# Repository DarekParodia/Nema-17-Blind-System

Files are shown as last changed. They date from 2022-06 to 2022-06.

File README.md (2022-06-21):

# Nema-17-Blind-System
I made my own system, for controling window blinds, using **Nema 17** stepper motor, and **a4988** stepper driver.
Design involves 3d printing, and making homemade pcb, or just using unviersal one.
Blinds can be easly controlled either by buttons or external hardware. PCB has 5 pins coming out of it, which has all the voltages and button pins coming in to microcontroller.
To connect motor to the pcb i used 2mm goldpins, because my motor has this type of connector.
You can drive blinds using gearbox, it depends on how heavy your blinds are, or how strong is your motor.
Design uses M3 screws to assembly everything. I didn't put points for screwing the pcb so you can attach it anyway you want

STL files can be found also on thingiverse: https://www.thingiverse.com/thing:5415491

# 🛠 Needed Parts
- 1x Nema 17 motor
- 1x a4988 driver
- Switches
    - 2x microswitch
    - 1x quad dip switch
- IC
    - 1x attiny 13
    - 1x lm7805
- Connectors
    - 1x quad goldpins (2mm)
    - 1x fivefold goldpins (2,54mm)
    - 1x dc jack (5.5mm)
- 2x capacitor (12v 100f)
- resistors
    -  2x 1 kΩ
    -  1x 470 Ω
- 1x 3mm led
- 1x 62x42 mm pcb  
- 12v power supply 1A (motor don't needs that much power but it's better to have more)
# 🔧 Assembly
- 3d print all needed parts
    - motor mount
    - blind holder
    - gearbox (Optional)
- screw motor to the motor mount (Optional: screw it with the gearbox)
- put on the tip blind holder
- screw all thing to the wall

# 🧩 Code
coming soon

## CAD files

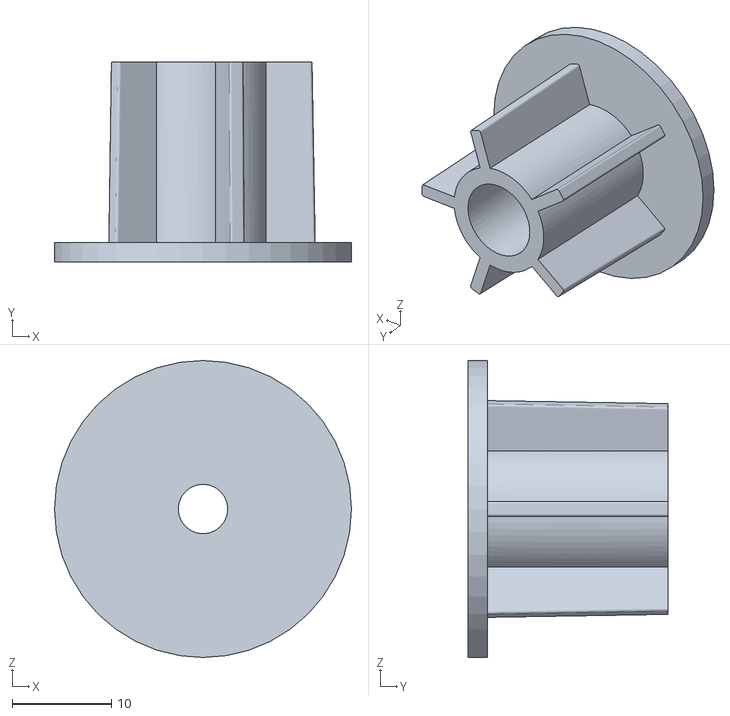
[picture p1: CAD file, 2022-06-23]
STL files/Blinds Holder v2.obj
30.0 x 20.3 x 30.0

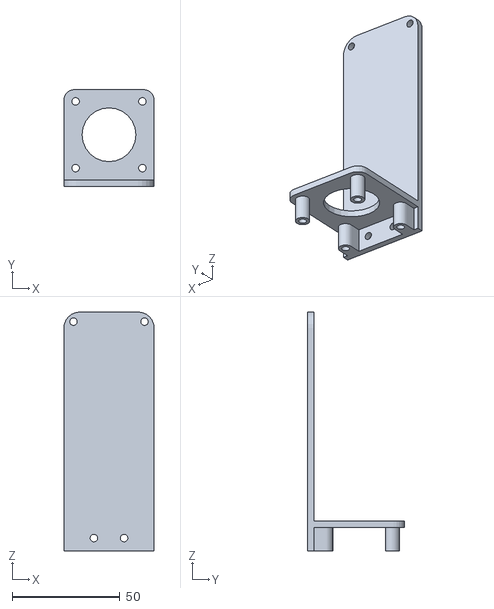
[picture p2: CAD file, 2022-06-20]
STL files/MotorMount v2.obj
42.0 x 45.0 x 111.0

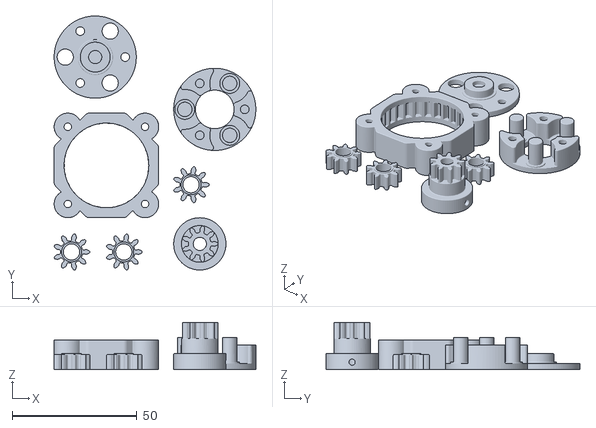
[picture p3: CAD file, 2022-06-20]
STL files/Planetary_Gearbox_v5_sep.stl
81.0 x 102.0 x 19.0

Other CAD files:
Fusion 360 files/MotorMount v2.f3d

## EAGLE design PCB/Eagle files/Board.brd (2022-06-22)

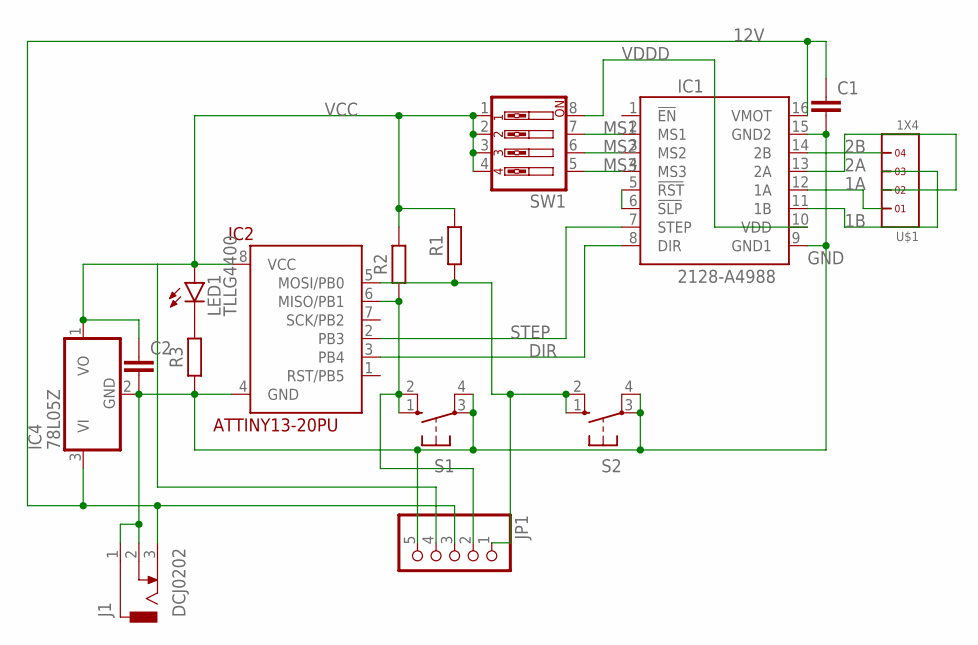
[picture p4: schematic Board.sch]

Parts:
C1, C2: C2.5/6; C2.5-6
IC1: 2128-A4988; A4988
IC2: ATTINY13-20PU; DIL08
IC4: 78L05Z; TO92
J1: DCJ0202
JP1: PINHD-1X5; 1X05
LED1: TLLG4400; LED3MM
R1, R2, R3: R_AXIAL-7.2MM-PITCH; RESAD724W46L381D178B
S1, S2: 10-XX; B3F-10XX
SW1: SW_DIP-4; EDG-04
U$1: 1X4

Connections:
1A: IC1.12 (1A), U$1.1
1B: IC1.11 (1B), U$1.3
2A: IC1.13 (2A), U$1.2
2B: IC1.14 (2B), U$1.4
12V: C1.1, IC1.16 (VMOT), IC4.3 (VI), J1.3, JP1.3
DIR: IC1.8 (DIR), IC2.3 (PB4)
GND: C1.2, C2.2, IC1.9 (GND1), IC1.15 (GND2), IC2.4 (GND), IC4.2 (GND), J1.1, J1.2, JP1.5, R3.1, S1.3, S1.4 (P1), S2.3, S2.4 (P1)
MS1: IC1.2 (MS1), SW1.7
MS2: IC1.3 (MS2), SW1.6
MS3: IC1.4 (MS3), SW1.5
unnamed: LED1.K (C), R3.2
unnamed: IC2.5 (MOSI/PB0), JP1.1, R1.1, S2.1 (S), S2.2 (S1)
unnamed: IC1.5 (!RST), IC1.6 (!SLP)
PB1: IC2.6 (MISO/PB1), JP1.2, R2.1, S1.1 (S), S1.2 (S1)
STEP: IC1.7 (STEP), IC2.2 (PB3)
VCC: C2.1, IC2.8 (VCC), IC4.1 (VO), JP1.4, LED1.A, R1.2, R2.2, SW1.1, SW1.2, SW1.3, SW1.4
VDDD: IC1.10 (VDD), SW1.8

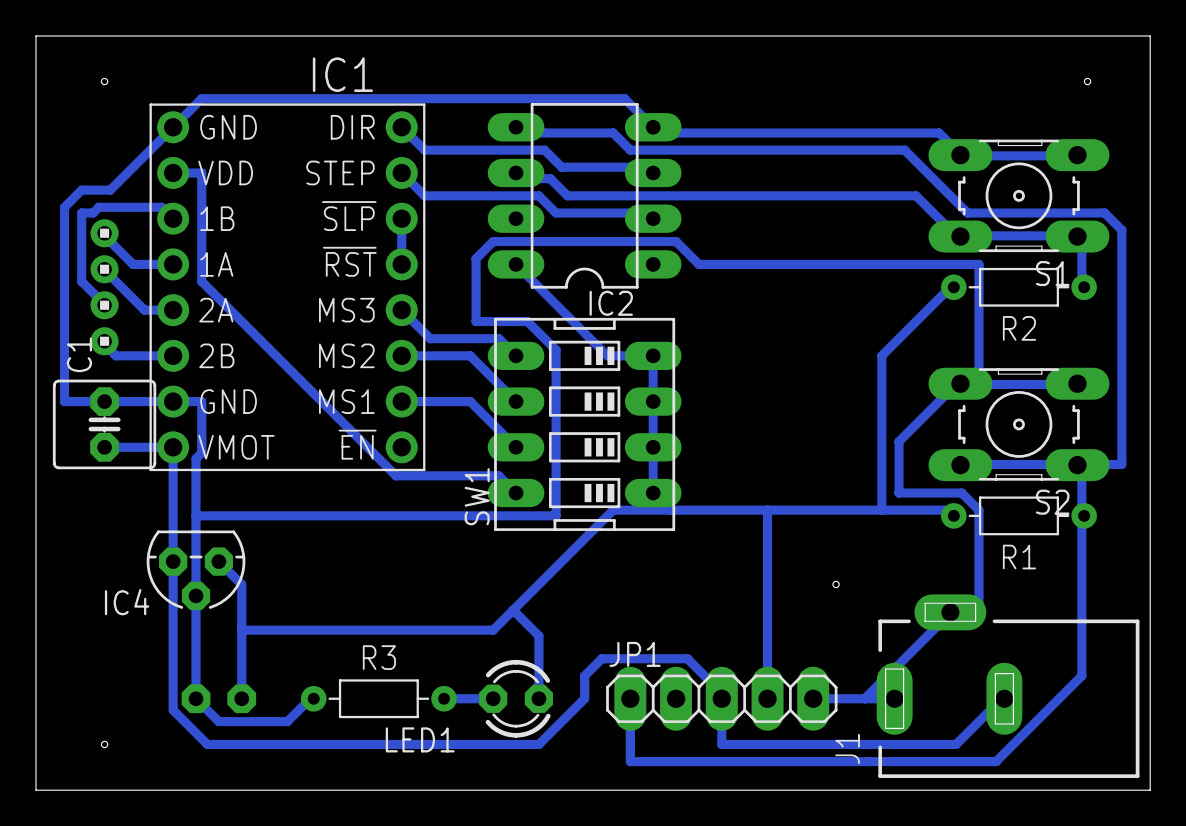
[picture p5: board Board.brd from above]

Board: 2 copper layers, 61.9 x 41.9 mm, 15 parts (1 on the bottom side), 17 nets.
